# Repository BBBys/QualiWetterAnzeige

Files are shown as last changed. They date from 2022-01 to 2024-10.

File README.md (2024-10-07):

# Qualitative Weather Display
QualiWetterAnzeige
## Goal
Display weather data like
temperature, pressure, humidity, wind, moon phase not as numeric, but as qualitative values such as high/low, strong/weak ... by pointers over a scale, each driven by a servo motor.
## Measured values and illustration
Temperature, relative humidity, air pressure and wind speed are taken into account.
The conversion should be carried out in such a way that
- the entire scale of the display (0° ... 180°) is used
- the average (mediam) value<sup>(2)</sup> is displayed by the pointer in 90° position.
### Example
* the air humidity (relative humidity r.h.) reaches 93 to 100% r.h. when it rains, but rarely<sup>(1)</sup> falls below 40% r.h. and never<sup>(1)</sup> below 13% r.h.
* Pointer position at 13 % r.h. --> 0° (i.e. left edge)
* Pointer position at 40 % RH --> 9°
* Pointer position at 93 % RH --> 171°
* Pointer position at 100 % RH --> 180° (right edge)
* Furthermore, the measured values are below 81% half the time<sup>(1)(2)</sup>
* Pointer position at 81 % RH --> 90° (i.e. middle)
## Adjustment
Since the values are partly dependent on the season,
- Temperature in summer and autumn higher than in spring and winter
- Humidity in spring and summer lower than in autumn and winter
the conversion is also adjusted (the differences in air pressure and wind speed are not statistically significant<sup>(1)</sup>)

* (1) Approx. 16,000 measured values were evaluated at hourly intervals from May 2019 to March 2021
* (2) Median value
-------------------
# Qualitative Wetteranzeige
QualiWetterAnzeige
## Ziel
Anzeige von Wetterdaten wie 
Temperatur, Druck, Feuchte, Wind, Mondphase als qualitative Werte wie hoch/niedrig, stark/schwach ... durch Zeiger über je einer Skala, angetrieben von Servo-Motoren
## Messwerte und Abbildung
Berücksichtigt werden Temperatur, relative Luftfeuchte, Luftdruck und Windeschwindigkeit

Dabei soll die Umrechnung so vorgenommen werden, dass 
  -   der gesammte Stellbereich (0° ... 180°) ausgenutzt wird
  -   der mittlere (Median) Wert<sup>(2)</sup>  durch den Zeiger in der als 90°-Stellung angezeigt wird.
 ### Beispiel
 * die Luftfeuchte (relative Feuchte r.F.) erreicht bei Regen 93 bis 100 % r.F., fällt aber selten<sup>(1)</sup> unter 40 % r.F. und nie(1) unter 13 % r.F.
 * Zeigerstellung bei  13 % r.F. -->   0° (also linker Rand)
 * Zeigerstellung bei  40 % r.F. -->   9°
 * Zeigerstellung bei  93 % r.F. --> 171°
 * Zeigerstellung bei 100 % r.F. --> 180° (rechter Rand)
 * weiter liegen die Messwerte in der Hälfte der Zeit(1) unter 81 % <sup>(2)</sup>
 * Zeigerstellung bei  81 % r.F. -->  90° (also Mitte)
## Anpassung
Da die Werte zum Teil von der Jahreszeit abhängig sind, 
 -    Temperatur im Sommer und Herbst höher als im Frühling und Winter
 -    Luftfeuchte im Frühling und Sommer niedriger als im Herbst und Winter

wird die Umrechnung auch angepasst (die Unterschiede bei Luftdruck und Windgeschwindigkeit sind statistisch<sup>(1)</sup> nicht signifikant)

* (1) ausgewertet wurden ca. 16.000 Messwerte in stündlichem Abstand von Mai 2019 bis März 2021
* (2) Medianwert

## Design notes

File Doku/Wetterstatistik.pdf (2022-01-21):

# Wetterstatistik

Rohdaten: 16 K Messwerte stündlich von Mai 2019 bis März 2021

# Jahreszeiten

Nach Tagen im Jahr.
- Tag 60 … 150: Frühling
- Tag 151 … 242: Sommer
- Tag 243 … 333: Herbst
- Tag 334 … 59: Winter
ANOVA für Temperatur, Feuchte, Windgeschwindigkeit und Druck: Mittelwerte signifikant unterschiedlich, F für Temperatur und Feuchte hoch, Windgeschwindigkeit und Druck deutlich kleiner.

# Temperatur [° C]

Perzentile ganzes Jahr
| min | 5 | 10 | 25 | 50 | 75 | 90 | 95 | max
temp | -19,7 | -0,2 | 1,2 | 4,3 | 10,0 | 16,0 | 20,9 | 23,6 | 36,4
Anzeige [°] | 0 | 9 | 18 | 45 | 90 | 135 | 162 | 171 | 180

Perzentile nach Jahreszeit
| Jahreszeit | Min | 5 | 10 | 25 | 50 | 75 | 90 | 95 | Max | Sp.W
temp | Frühling | -5.6 | 0.0 | 1.6 | 4.4 | 8.0 | 12.9 | 17.0 | 19.1 | 22.9 | 28.5
| Sommer | 6.4 | 11.0 | 12.5 | 14.9 | 18.2 | 21.8 | 25.4 | 27.9 | 36.4 | 30.0
| Herbst | -1.9 | 2.5 | 3.7 | 6.9 | 10.6 | 14.1 | 17.5 | 19.7 | 31.2 | 33.1
| Winter | -19.7 | -3.4 | -1.1 | 0.9 | 3.0 | 5.7 | 8.3 | 9.9 | 17.4 | 37.1

Einstufung:
| Sehr kalt < | Kalt < | Warm > | Sehr warm >
Frühling | 0,0 | 4,4 | 12,9 | 19,1
Sommer | 11,0 | 14,9 | 21,8 | 27,9
Herbst | 2,5 | 6,9 | 14,1 | 19,7
Winter | -3,4 | 0,9 | 5,7 | 9,9

# Luftfeuchtigkeit [% rel.]

Perzentile ganzes Jahr
| Min | 5 | 10 | 25 | 50 | 75 | 90 | 95 | Max
feucht | 13 | 40 | 48 | 66 | 81 | 89 | 93 | 100 | 100
Anzeigewinkel (0…180) | 0° | 9° | 19° | 47° | 95° | 142° | 171° | 180° | 180°

Perzentile nach Jahreszeit
| Jahreszeit | 5 | 10 | 25 | 50 | 75 | 90 | 95
feucht | Frühling | 32 | 37 | 50 | 70 | 86 | 93 | 93
| Sommer | 37 | 42 | 53 | 69 | 83 | 93 | 93
| Herbst | 49 | 60 | 75 | 83 | 93 | 93 | 100

2

Winter | 64 | 69 | 79 | 86 | 93 | 96 | 100

Einstufung:
| Sehr trocken | Trocken | Feucht | Sehr feucht
Frühling | 32 | 50 | 89 | 93
Sommer | 37 | 53 | 89 | 93
Herbst | 40 | 66 | 93 | 100
Winter | 40 | 66 | 93 | 100

## Luftdruck [hPa]

Perzentile ganzes Jahr
| Min | 5 | 10 | 25 | 50 | 75 | 90 | 95 | Max
druck | 976 | 996 | 1002 | 1010 | 1016 | 1021 | 1026 | 1030 | 1047
Anzeige [°] | 0 | 9 | 18 | 45 | 90 | 135 | 162 | 171 | 180

Perzentile nach Jahreszeit
| Jahreszeit | 5 | 10 | 25 | 50 | 75 | 90 | 95
druck | Frühling | 999 | 1004 | 1012 | 1019 | 1024 | 1029 | 1032
| Sommer | 1007 | 1009 | 1012 | 1016 | 1019 | 1023 | 1025
| Herbst | 997 | 1002 | 1008 | 1015 | 1021 | 1026 | 1028
| Winter | 992 | 996 | 1004 | 1014 | 1022 | 1031 | 1035

Einstufung:
| Sehr niedrig | Niedrig | Hoch | Sehr hoch
Frühling | 996 | 1010 | 1024 | 1032
Sommer | 996 | 1010 | 1021 | 1030
Herbst | 996 | 1008 | 1021 | 1030
Winter | 992 | 1004 | 1022 | 1035

# Wind [m/s]

Perzentile
| Min | 5 | 10 | 25 | 50 | 75 | 90 | 95 | Max
windv | 0,1 | ,5 | 1,0 | 1,5 | 3,1 | 4,6 | 6,2 | 7,2 | 17,0
Anzeige [°] | 0 | 9 | 18 | 45 | 90 | 135 | 162 | 171 | 180

Unabhängig von Jahreszeit
Einstufung
3…5 | 5…15 | 15…24 | 24…
Schwacher Wind | Starker Wind | Sturm | Starker Sturm

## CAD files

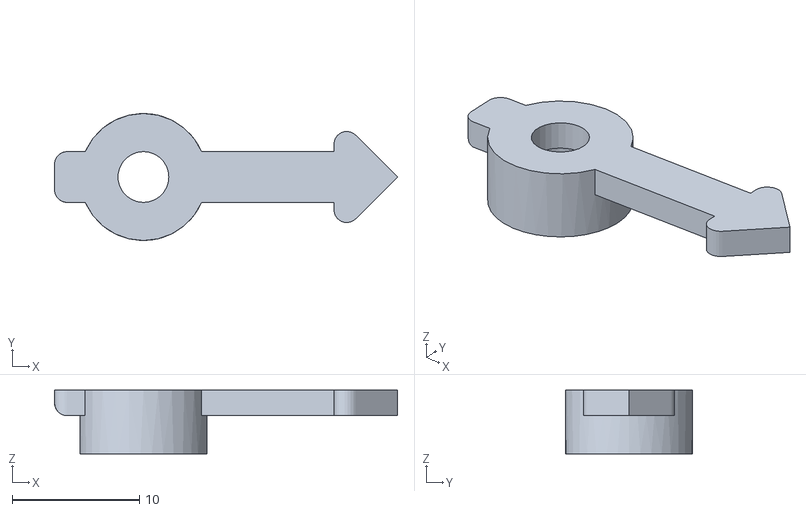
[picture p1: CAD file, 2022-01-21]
Hardware/Zeiger.stl
27.0 x 10.0 x 5.00

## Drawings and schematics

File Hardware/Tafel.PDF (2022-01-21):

100,0
50,0

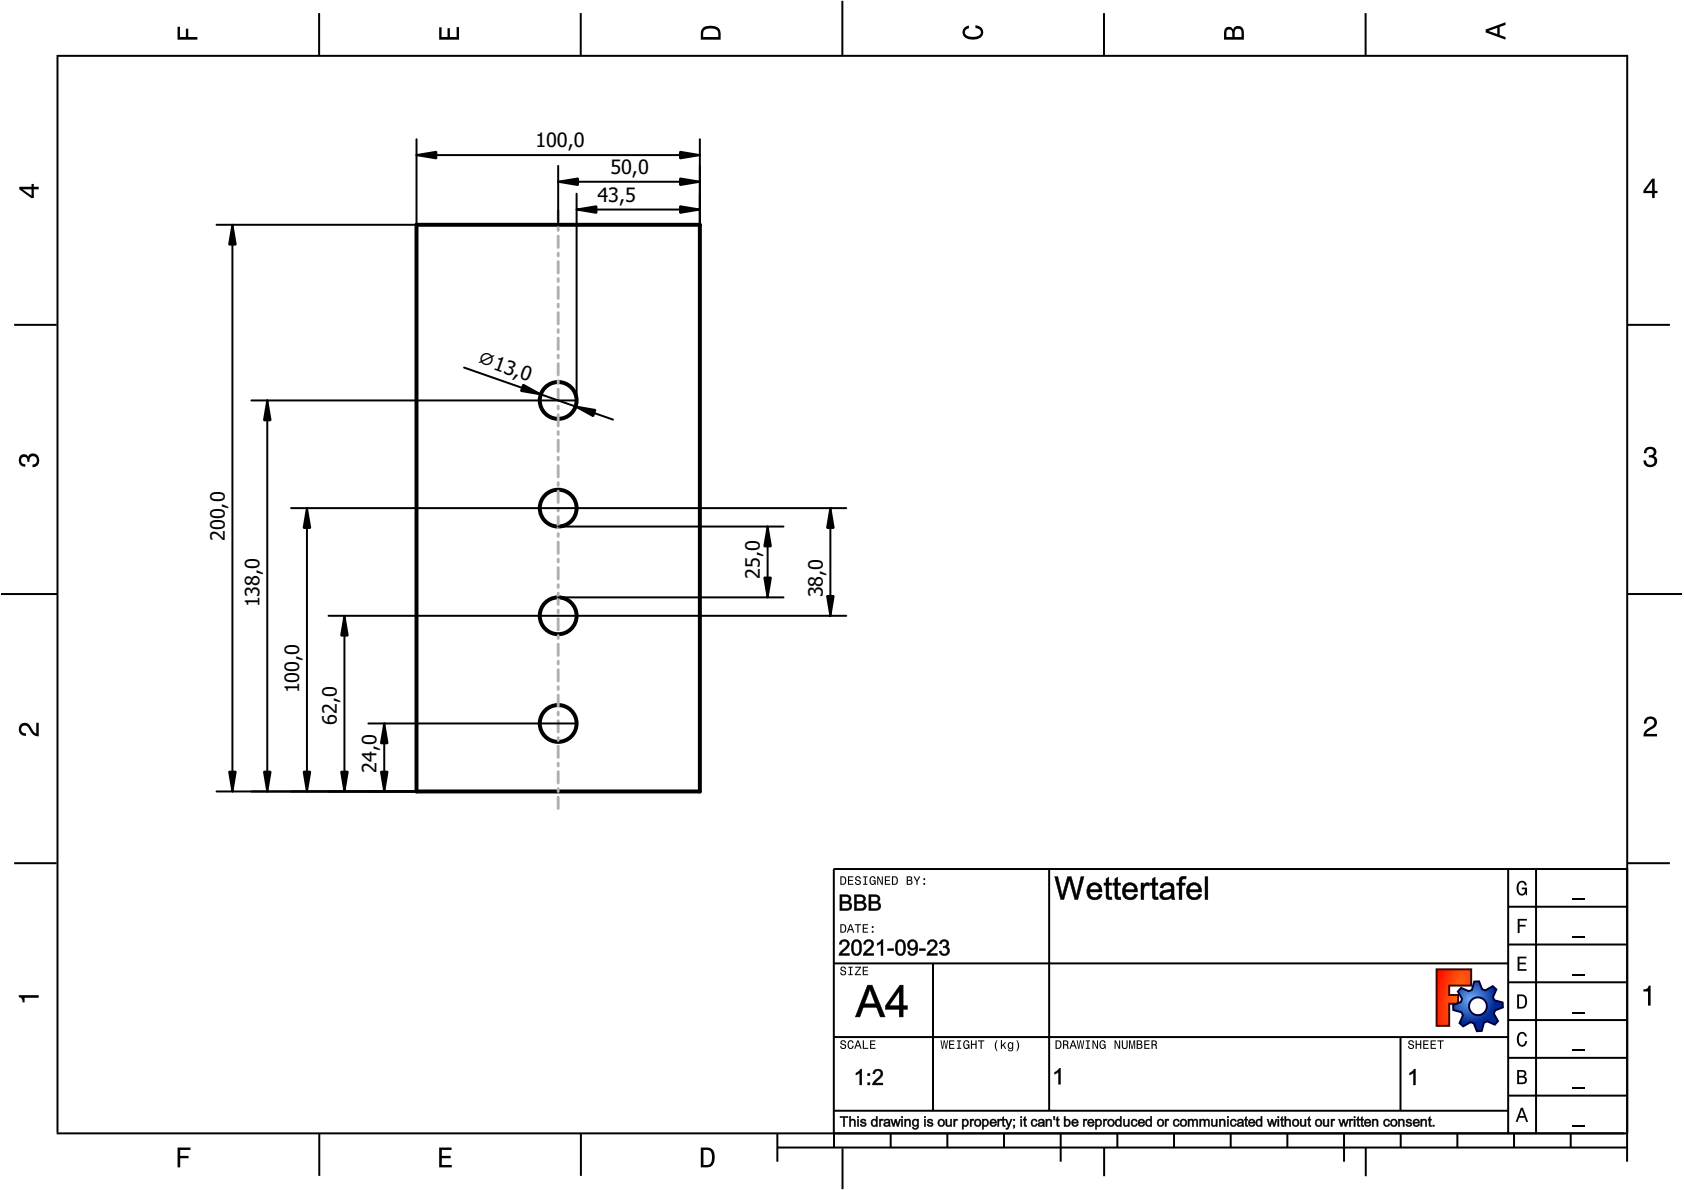
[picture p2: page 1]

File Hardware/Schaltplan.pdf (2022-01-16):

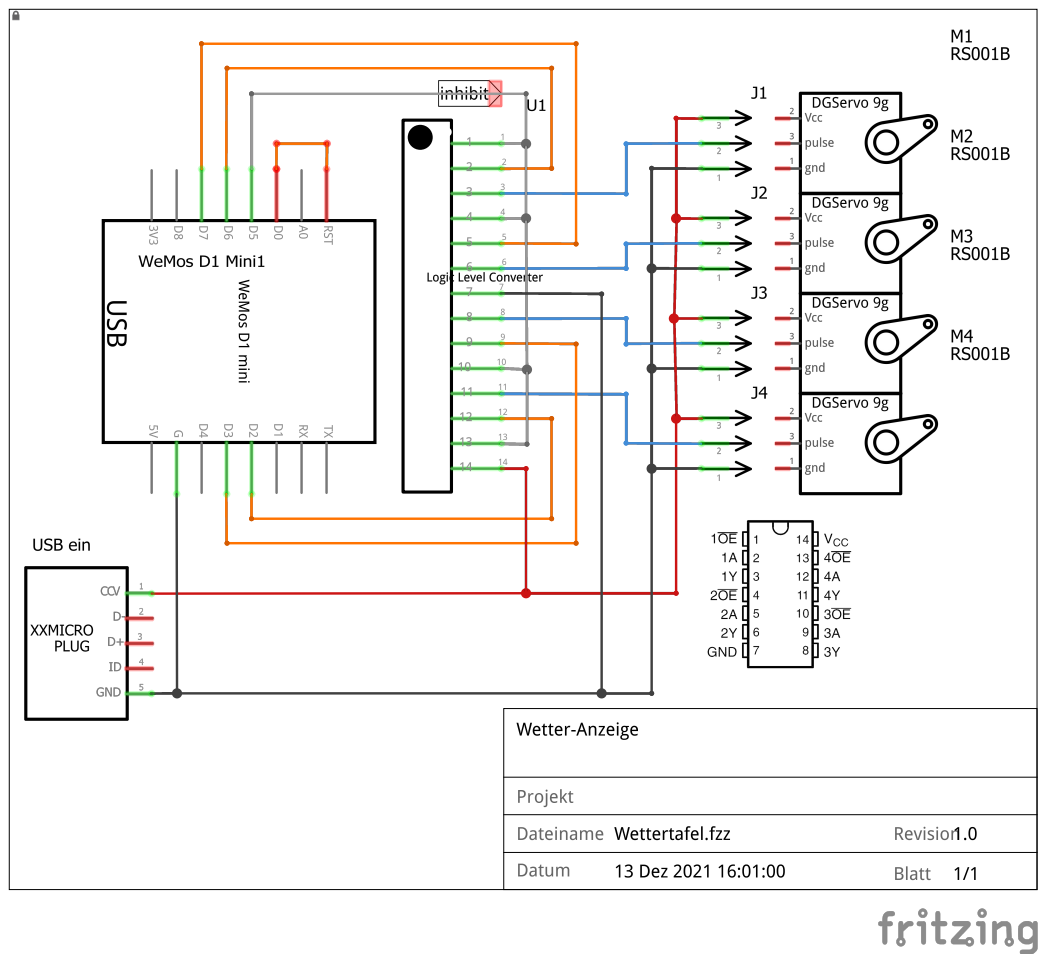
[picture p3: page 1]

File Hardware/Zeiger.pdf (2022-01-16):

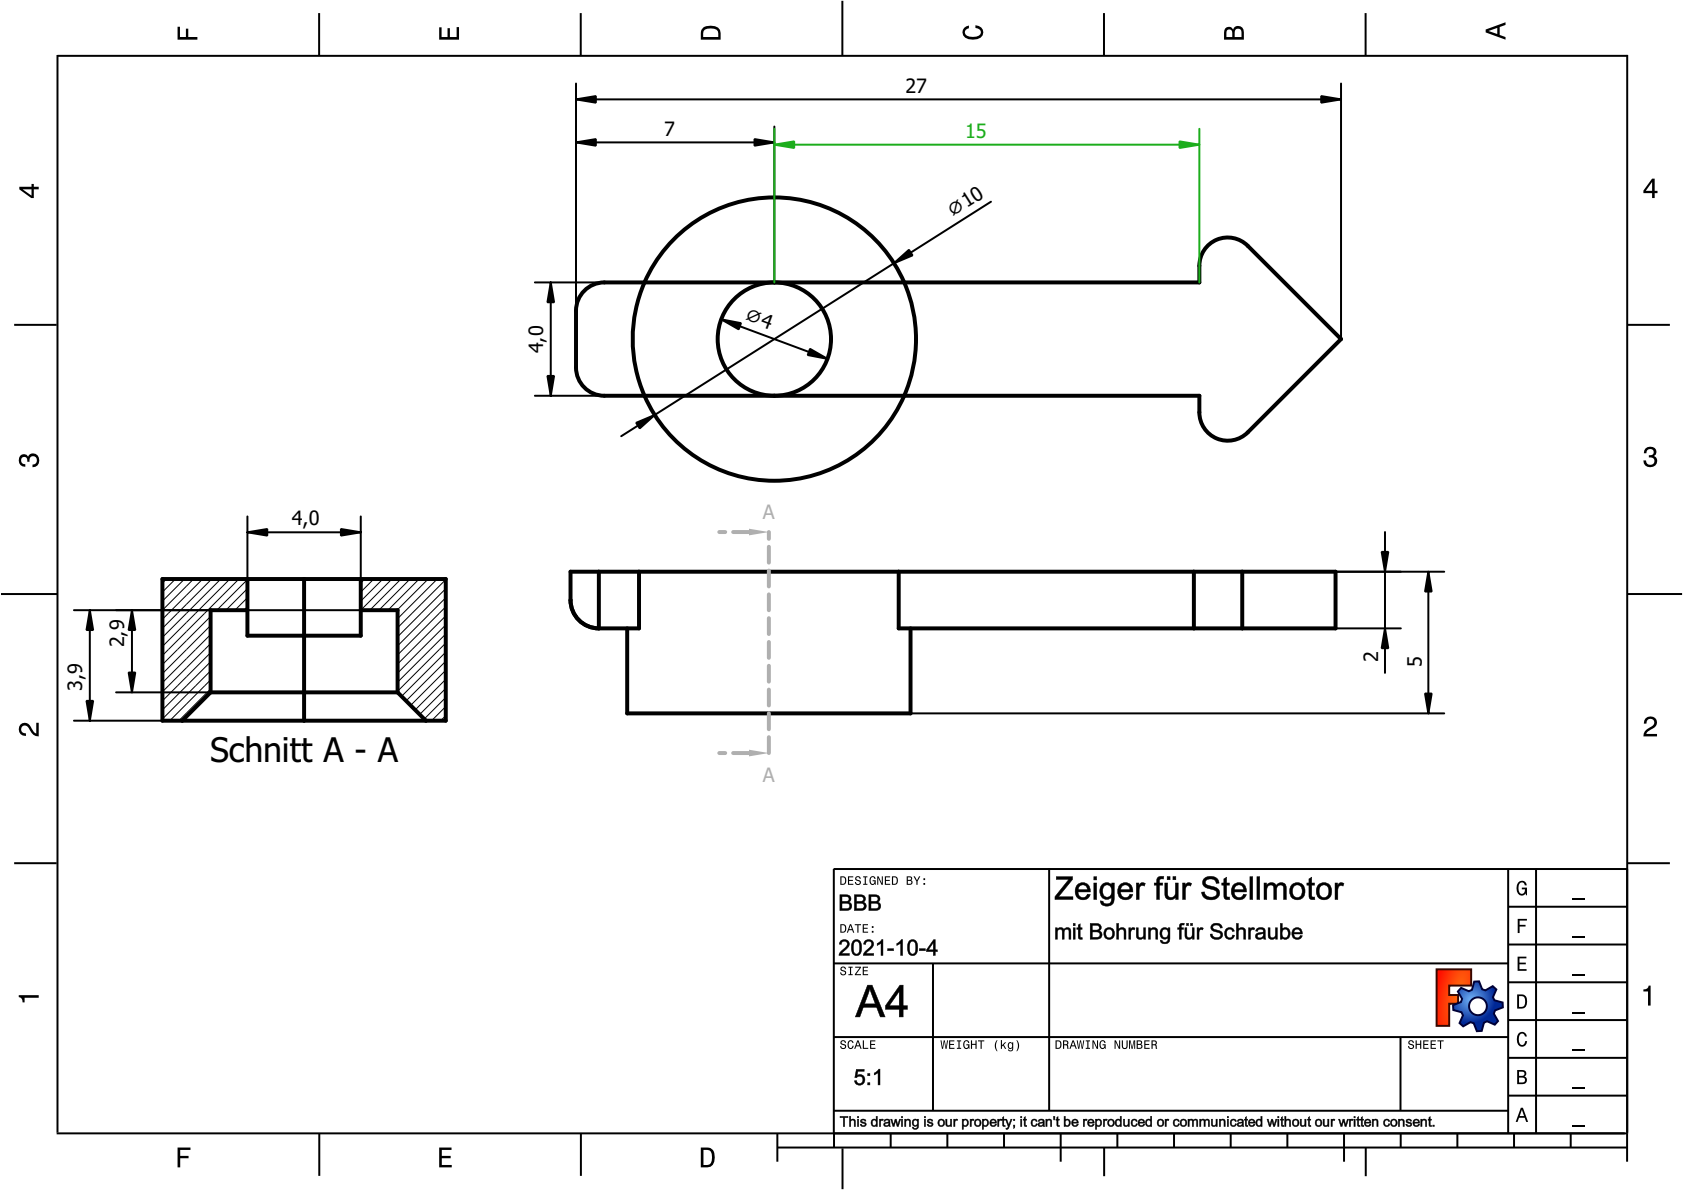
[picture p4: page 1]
nitt A - A ⁴,0

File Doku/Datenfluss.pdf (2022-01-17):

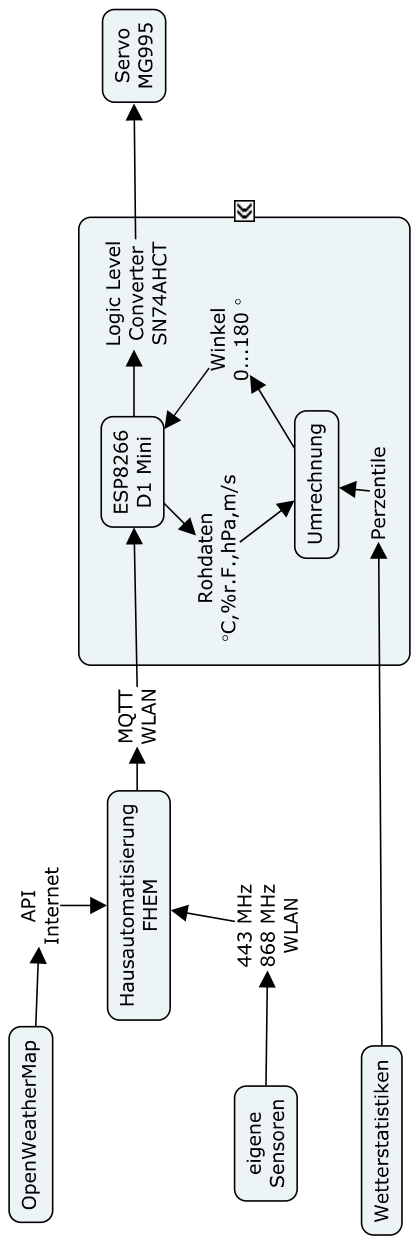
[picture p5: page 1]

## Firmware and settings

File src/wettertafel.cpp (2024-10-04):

/**
 * @file wettertafel.cpp
 * Qualitative Anzeige von Wetterdaten auf einer Wettertafel über Servo-Motoren
 * ============================================================================
 * @author Dr. Burkhard Borys, Zeller Ring 15, 34246 Vellmar, Deutschland
<<<<<<< Updated upstream
 * @version 1.1
 * @date 21 16 Jan 2022 16 Dez 21 20 Nov 26 Okt 30 19 Sep 2021
=======
 * @version 2.1
 * @date 18 17 15 9 Aug 25 Feb 21 16 Jan 2022 16 Dez 21 20 Nov 26 Okt 30 19 Sep 2021
>>>>>>> Stashed changes
 * @copyright Copyright (c) 2021-2022 B. Borys
 * @note Verwendeter Beispielcode von Adafruit:
 *   Written by Limor Fried/Ladyada for Adafruit Industries.
 */

#include "wettertafel.h"
#include <Ticker.h> // Load library "ticker"
extern uint8_t Jahreszeit, WinkelF, WinkelT, WinkelD, WinkelW, WinkelM;
/// Servo?
#ifdef SERVO
extern Servo ZeigerT, ZeigerF, ZeigerD, ZeigerW, ZeigerM; // create servo object to control a servo
<<<<<<< Updated upstream
#endif        // Servo
=======
#else
#include <Adafruit_PWMServoDriver.h>
// called this way, it uses the default address 0x40
Adafruit_PWMServoDriver pwm = Adafruit_PWMServoDriver();
#endif // Servo
>>>>>>> Stashed changes

/**
 * @brief blinken
 * 
 */
Ticker Zeitgeber;

#ifdef MQTTein
#include "EspMQTTClient.h"
/*
   ================================================================================================
   MQTT
*/

/**
 * @brief MQTT
 * 
 */
EspMQTTClient MQTTClient(
    WLANSSID,
    WLANPWD,
    MQTTBROKERIP, // MQTT Broker server ip
    OTAUSER,      // Can be omitted if not needed
    OTAPASSWD,    // Can be omitted if not needed
    MQTTNAME,     // Client name that uniquely identify your device
    1883          // The MQTT port, default to 1883. this line can be omitted
);
/*
   MQTT
   ====================================================================================================
*/
#endif

/**
 * @brief Servo aus und 15 Minuten schlafen legen
 * Quelle: https://raw.githubusercontent.com/RuiSantosdotme/ESP32-Course/master/code/DeepSleep/TimerWakeUp/TimerWakeUp.ino
 */
void schlafen()
{
#ifndef NDEBUG
  Serial.println("schlafen");
  Serial.flush();
#endif
#ifdef SERVO
  ZeigerF.detach();
  ZeigerT.detach();
  ZeigerD.detach();
  ZeigerW.detach();
  ZeigerM.detach();
#endif
  delay(1000);
#ifdef NDEBUG
  ESP.deepSleep(991000000L);
#else
  ESP.deepSleep(5000000L);
#endif
  delay(1000);
  //yield();
}

/**
 * @brief Messdaten über MQTT anfordern
 * 
 */
void onConnectionEstablished()
{
<<<<<<< Updated upstream
#ifndef NDEBUG
  Serial.println("onConnectionEstablished");
#endif
  WinkelW = Stellen(ZeigerW, WinkelW, 100);
=======
DbgsOut("onConnectionEstablished");
  WinkelW = Stellen  (ZeigerW, WinkelW, 100);
>>>>>>> Stashed changes
#ifdef MQTTein
  MQTTClient.subscribe("Datum/JZeit", [](const String &payload)
                   { Jahreszeit = payload.toInt(); });
  MQTTClient.subscribe("Wetter/Feuchte", [](const String &payload)
                   { AnzeigenF(payload.toInt()); });
  MQTTClient.subscribe("Wetter/Wind", [](const String &payload)
                   { AnzeigenW(payload.toFloat()); });
  MQTTClient.subscribe("Temp/Aussen", [](const String &payload)
                   { AnzeigenT(payload.toFloat()); });
  MQTTClient.subscribe("Wetter/Druck", [](const String &payload)
                   { AnzeigenD(payload.toInt()); });
  MQTTClient.subscribe("Datum/MondN", [](const String &payload)
                       { AnzeigenM(payload.toFloat()); });
  // MQTTClient.subscribe("ein", [](const String &payload)
  //                      { digitalWrite(DISABLE, LOW); });
  // MQTTClient.subscribe("aus", [](const String &payload)
  //                      { digitalWrite(DISABLE, HIGH); });
  MQTTClient.subscribe("Wettertafel/direkt", [](const String &payload) { /// direktes Stellen zum Testen
    int w = payload.toInt();
    WinkelF = Stellen(ZeigerF, WinkelF,w );
    WinkelT = Stellen(ZeigerT, WinkelT, w);
    WinkelD = Stellen(ZeigerD, WinkelD, w);
    WinkelW = Stellen(ZeigerW, WinkelW, w);
    WinkelM = Stellen(ZeigerM, WinkelM, w);
#ifndef NDEBUG
    Serial.println("...direkt fertig");
#endif
  });
  MQTTClient.publish("SWVersion", VERSION);
  MQTTClient.publish("SWDatum", __DATE__);
  MQTTClient.publish("OTA-Usr", OTAUSER);
  MQTTClient.publish("OTA-Pwd", OTAPASSWD);
  MQTTClient.publish("Status", "Wettertafel läuft");
  MQTTClient.publish("Abfrage", "jetzt"); ///trigger die sofortige Übertragung der Daten
  Zeitgeber.detach();
  digitalWrite(LED_BUILTIN, LED_EIN); //ein
#endif                                //MQTTein
#ifndef NDEBUG
  Serial.println("... onConnectionEstablished return");
#endif
  WinkelW = Stellen(ZeigerW, WinkelW, 90);
} //void onConnectionEstablished()
/**
 * @brief LED blinken lassen
 * 
 */
void flip()
{
  digitalWrite(LED_BUILTIN, !digitalRead(LED_BUILTIN));
}

void setup()
{
#ifndef NDEBUG
  Serial.begin(115200);
  Serial.println("\n...setup");
#endif
      pinMode(LED_BUILTIN, OUTPUT);
  // pinMode(DISABLE, OUTPUT);
  Zeitgeber.attach(.5, flip);
#ifdef SERVO
#ifndef NDEBUG
  Serial.println("Attach Servos");
#endif
  /*
 * Achtung: 1 (=TX) und 7 (=?) funktioniert nicht
 * PWM-Ports für D1_Mini: D1..8, TX und RX
 * verwendet: D2, D3, D6, D7
 * D1, D8 geht auch, D5 sollte auch gehen
 * D4 hängt mit der LED zusammen?
 */
  ZeigerF.attach(D1, 500, 2500);
  ZeigerM.attach(D2, 500, 2500);
  ZeigerT.attach(D6, 500, 2500);
  ZeigerD.attach(D3, 500, 2500);
  ZeigerW.attach(D8, 500, 2500);
#ifndef NDEBUG
  Serial.println("Servos OK");
  WinkelT = Stellen(ZeigerT, WinkelT, 0);
  WinkelF = Stellen(ZeigerF, WinkelF, 0);
  WinkelD = Stellen(ZeigerD, WinkelD, 0);
  WinkelW = Stellen(ZeigerW, WinkelW, 0);
#endif
<<<<<<< Updated upstream
#endif //SERVOS
=======
#else //SERVO

  pwm.begin();
      /*
     * In theory the internal oscillator (clock) is 25MHz but it really isn't
     * that precise. You can 'calibrate' this by tweaking this number until
     * you get the PWM update frequency you're expecting!
     * The int.osc. for the PCA9685 chip is a range between about 23-27MHz and
     * is used for calculating things like writeMicroseconds()
     * Analog servos run at ~50 Hz updates, It is importaint to use an
     * oscilloscope in setting the int.osc frequency for the I2C PCA9685 chip.
     * 1) Attach the oscilloscope to one of the PWM signal pins and ground on
     *    the I2C PCA9685 chip you are setting the value for.
     * 2) Adjust setOscillatorFrequency() until the PWM update frequency is the
     *    expected value (50Hz for most ESCs)
     * Setting the value here is specific to each individual I2C PCA9685 chip and
     * affects the calculations for the PWM update frequency.
     * Failure to correctly set the int.osc value will cause unexpected PWM results
     */
  pwm.wakeup();
  pwm.setOscillatorFrequency(26645063L); // Kalibriert 2022-08-17
  pwm.setPWMFreq(SERVO_FREQ);            // Analog servos run at ~50 Hz updates
#endif //SERVO
  delay(10);
>>>>>>> Stashed changes
#ifdef MQTTein
#ifdef NDEBUG
  MQTTClient.enableDebuggingMessages(false);
#else                            //NDEBUG
  MQTTClient.enableDebuggingMessages(true);
  // digitalWrite(DISABLE, LOW);
  WinkelT = Stellen(ZeigerT, WinkelT, 90);
  WinkelF = Stellen(ZeigerF, WinkelF, 90);
#endif                           //NDEBUG
  MQTTClient.enableHTTPWebUpdater(); // Enable the web updater. User and password default to values of MQTTUsername and MQTTPassword.
  MQTTClient.enableLastWillMessage("Wettertafel/lastwill", "Abbruch Wettertafel"); /// LWT-Meldung
#endif                                                                         //MQTTein
#ifndef NDEBUG
  Serial.println("Setup OK");
  WinkelD = Stellen(ZeigerD, WinkelD, 90);
  WinkelW = Stellen(ZeigerW, WinkelW, 90);
  WinkelM = Stellen(ZeigerM, WinkelM, 90);
#endif
}

void loop()
{
#ifdef MQTTein
  MQTTClient.loop();
  //if (!MQTTClient.isConnected())    Serial.println("!connected");
  //if (!MQTTClient.isWifiConnected())    Serial.println("!WIFIconnected");
  //if (!MQTTClient.isMqttConnected () )Serial.println("!MQTTconnected");
#endif
  delay(100);
}

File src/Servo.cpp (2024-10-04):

/**
 * @file Servo.cpp
 * @brief alle Servo-Routinen
 * @author Dr. Burkhard Borys, Zeller Ring 15, 34246 Vellmar, Deutschland
<<<<<<< Updated upstream
 * @version 1.1
 * @date 16 Jan 2022  16 Dez 21 Nov 26 Okt 30 19 Sep 2021
=======
 * @version 2.1
 * @date 18 17 15 9 Aug 25 Feb 16 Jan 2022  16 Dez 21 Nov 26 Okt 30 19 Sep 2021
>>>>>>> Stashed changes
 * 
 * @copyright Copyright (c) 2021-2022 B. Borys
 * 
 */
#include "wettertafel.h"
#ifdef SERVO
/**
 * @brief stellt Servo auf Winkel, beschränkt auf 0...180
 * 
 * @param Servo, Winkel, neuer Winkel, Verzögerung
 */
int Stellen(Servo Zeiger, int ist,int winkel, const int DELAY)
{
    int ziel;
    ziel = max(min(winkel, 180), 0);
#ifndef NDEBUG
    Serial.print("Anzeigen Winkel: ist=");
    Serial.println(ist);
    Serial.print("................Ziel=");
    Serial.println(ziel);
    //const int DELAY = 30;
#else
    //const int DELAY = 17;
#endif
if (DELAY>0)
{
    for (uint8 i = 0; i < 180; i++)
    {
        flip();
        delay(DELAY);
        if (ziel > ist)
            ist++;
        else if (ziel < ist)
            ist--;
        else
            break;
        Zeiger.write(ist);
    }
}
    Zeiger.write(ziel);
#ifndef NDEBUG
    Serial.println("Ziel erreicht");
#endif
    digitalWrite(LED_BUILTIN, LED_AUS); //aus
    return ziel;
}
<<<<<<< Updated upstream
=======
#else   //SERVO
#include <Adafruit_PWMServoDriver.h>
// called this way, it uses the default address 0x40
extern Adafruit_PWMServoDriver pwm;
/**
 * @brief stellt Servo über Multiplexer PCA9685 auf Winkel, beschränkt auf 0...180
 *
 * @param Adresse des Servo 
 * @param Winkel
 * @param neuer Winkel
 * @param Verzögerung 
 */
int Stellen(int Zeiger, int ist, int winkel, const int DELAY)
{
    int ziel;
    int stellwert;
    ziel = max(min(winkel, 180), 0);
#ifndef NDEBUG
    Serial.print("Anzeigen Winkel: ist=");
    Serial.println(ist);
    Serial.print("              Zeiger=");
    Serial.println(Zeiger);
    Serial.print("................Ziel=");
    Serial.println(ziel);
    // const int DELAY = 30;
#else
    // const int DELAY = 17;
#endif
    // digitalWrite(DISABLE, LOW);
    // delay(500);
    pwm.wakeup();
    if (DELAY > 0)
    {
        for (uint8 i = 0; i < 180; i++)
        {
            flip();
            delay(DELAY);
            if (ziel > ist)
                ist++;
            else if (ziel < ist)
                ist--;
            else
                break;
            stellwert = dmap(ist, 0, 180, SERVOMIN, SERVOMAX);
            pwm.setPin(Zeiger, stellwert);
        }
    }
    digitalWrite(LED_BUILTIN, LED_EIN); // ein
    stellwert = dmap(ziel, 0, 180, SERVOMIN, SERVOMAX);
    pwm.setPin(Zeiger, stellwert);
DbgsOut("Ziel erreicht");
    digitalWrite(LED_BUILTIN, LED_AUS); // aus
    // delay(500);
    // digitalWrite(DISABLE, HIGH);
    pwm.sleep();
    return stellwert;
}
>>>>>>> Stashed changes
#endif

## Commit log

2022-01-16 Hardware
    Schaltplan und Zeiger
2022-01-18 Erläuterungen zum Umrechnung
    Erläuterungen zum Umrechnung der Messwerte in Zeigerstellung
2022-01-21 Mondphase
    neu: Code für Anzeige der Mondphase
2022-01-21 Hardware und Doku
    [Zeiger.stl]
